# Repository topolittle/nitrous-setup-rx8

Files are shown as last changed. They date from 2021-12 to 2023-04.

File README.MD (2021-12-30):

# Nitrous Oxide System installation for the Maxda RX-8

I wanted a nice and clean installation for my Nitrous Oxide System in my car. My installation has the following components:
- Main kit
- Bottle heater
- Purge
- NOS pressure sensor and gauge
- Fuel pressure sensor and gauge
- Oil pressure sensor and gauge
- Oil temperature sensor and gauge

Each components comes with wires and switches, so at the end of the day you end-up with a cockpit full of holes and different looking switches all over the place.

My goal for this project was to have all the system controls and gauges at the same place, under the original ashtray cover. I wanted also something that was easily serviceable. For example if I need to remove a sensor, I should be as easy as any other factory components.

There is two 3D printed components, one for the main control board and the other one for the head unit, in place of the ashtray. The parts were printed in ASA since it can support high and freezing temperature without deforming.

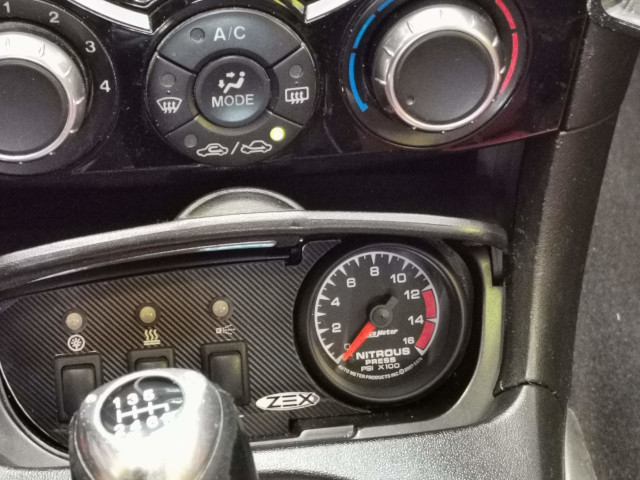
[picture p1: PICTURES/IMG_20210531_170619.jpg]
Ashtray


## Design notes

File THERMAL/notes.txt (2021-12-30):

Thermal managment:
Power to dissipate inside the enclosure: 200mA * 12V = 2.4W
Surface area of the enclosue: 0.4 ft-sqr
Watt per square foot: 6
Temperature rise: 15.5C (approx)
Expected max ambiant: 40C, so it gives us a max temperature of 55.5C inside the case,
just below of the glass transition temperature of the PLA which is 65C. ABS appears more suited for
this job since its glass transition temperature is around 105C.

Reference: https://safe.nrao.edu/wiki/pub/CICADA/GreenBankSpectrometer/Hoffman_Heat_Dissipation_Document.pdf

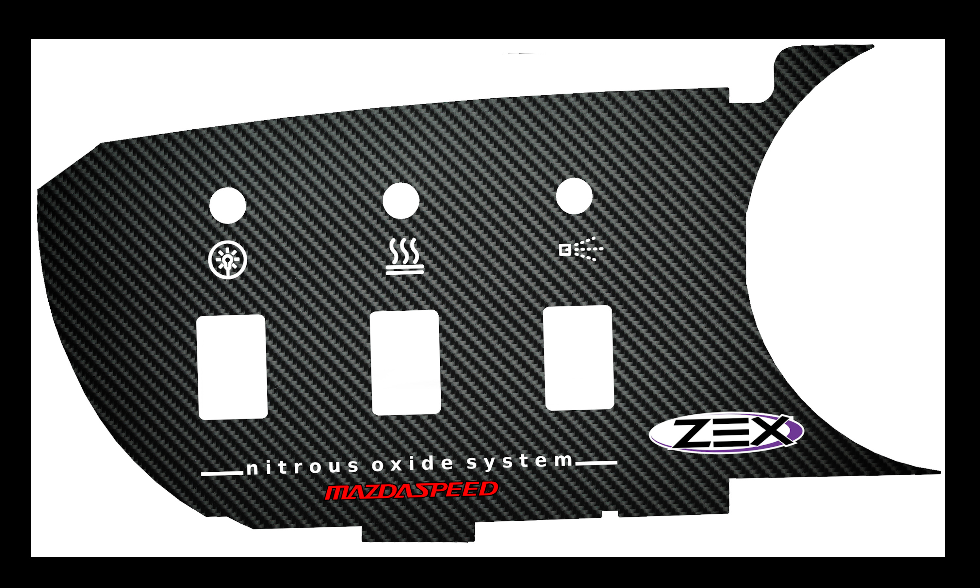
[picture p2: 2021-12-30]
ARTWORK/Nitrous_Artwork_v11_600dpi.jpg

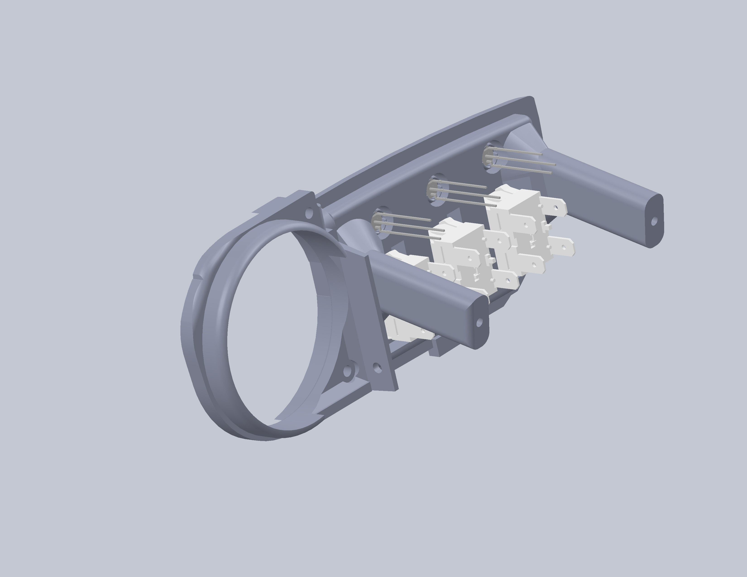
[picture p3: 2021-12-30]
MECHA/3D_MODEL/EXPORTS/front_panel_back.JPG

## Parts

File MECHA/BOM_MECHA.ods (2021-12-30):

Ordered | Where |  |  |  | Brand | Part No. | Autopartway | TDOT | Amazon | Garage16 | Notes
08/11/20 | Website | Lotek Gague pod w clamp and silicone | $100.00 | USD | Lo-Tek |  |  |  |  |  |  | http://www.gaugepods.com/mazda.html
08/12/20 | Garage16 | Prosport gauges oil pressure | $57.00 | USD | Prosport | 216BFWAOPSM.PSI | n/a | n/a | n/a | $104.50 |  | https://prosportgauges.com/collections/performance-series-amber-white/products/amber-white-2-1-16-electrical-oil-pressure-gauge
08/12/20 | Garage16 | Prosport gauges oil temp | $49.00 | USD | Prosport | 216BFWAOTSM.F |  |  | $85.00 | $85.00 |  | https://prosportgauges.com/collections/performance-series-amber-white/products/amber-white-2-1-16-electric-oil-temperature-gauge
08/18/20 | Garage16 | Prosport gauges fuel pressure
08/12/20 | Garage16 | Mishimoto Sandwish plate adaptor | $93.00 | CAD | Mishimoto | MMOP-TPS | n/a | $105.00 | $93.00 | $77.00 |  | https://www.mishimoto.com/oil-plate-sandwich-adapter.html#features | https://www.amazon.ca/-/fr/Mishimoto-MMOP-TPS-Sandwich-Plate-Adapter/dp/B004UVL6T4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
08/12/20 | Garage16 | Auto Meter 5974 Nitrous pressure gauge | $333.00 | CAD | Auto Meter | 5974 | 239 | 333 | 375 | 335 |  | https://www.tdotperformance.ca/auto-meter-5974-2-1-16-nitrous-0-1600-psi-es.html
08/20/20 | Julien | ZEX Nitrous kit 82021 | $950.00 | CAD |  |  | 924 |  |  |  |  | https://www.zex.com/wet-nitrous-system.html
08/12/20 | Garage16 | Vibrant 4 AN 1/8 npt adaptor | $13.00 | USD |  | 16484 | 16.63 | 40 | 40 | 21.12 | for nitrous line to pressure gauge | https://www.summitracing.com/parts/vpe-16484?seid=srese1
08/18/20 | Amazon | Aeromotive Fuel Line Adapter | $80.00 | USD |  | 15120 | n/a | n/a | $98.00 | n/a |  | https://black-halo-racing.myshopify.com/products/aeromotive-fuel-line-adapter
08/18/20 | Garage16 | vibrant 6an to 4an reducer |  |  |  | 10431
08/20/20 | Julien | Zex nitrous purge kit 82010 | $114.00 | USD |  |  |  |  |  |  |  | https://www.zex.com/nitrous-purge-kit.html
08/20/20 | Julien | Zex bottle heater 82006
 |  | Remote openner |  |  | Zex | 82009
08/17/20 | BHR | Throttle Body Spacer | 120 | USD
4 |  | M3 x 16mm button screw | for control unit enclosure
3 |  | M4 x 10mm button screw | for control unit pcb
2 |  | M3 x 10mm button screw | for head unit pcb
2 |  | M3 x 16mm button screw | for head unit fixation

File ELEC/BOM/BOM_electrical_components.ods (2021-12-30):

Qt | Part | Description | Digikey
3 | ACV31012 | RELAY AUTOMOTIVE SPST 20A 12V | 255-5270-ND
1 | G5V-1-2 DC12 | G5V-1-2 DC12 | Z3823-ND
1 | 1N4678 | Zener 1.8V | ‎641-MMSZ4678-HFCT-ND‎
1 | 2N3904
5 | 1N4007
4 | 4.7K | 1W | BC4534CT-ND
1 | 1K | 1/4W
1 | UBW1E101MPD1TD | 100uF/25V | 493-13149-1-ND
2 | FA26X8R1E105KNU06 | 1uF/25v Ceramic | 445-175056-1-ND
1 | PA414C1100 | SWITCH PUSH SPST-NO 16A 125V | PA414C1100-ND
2 | PA412C1100 | SWITCH PUSH DPST 16A 125V | EG4688-ND
3 | XLMDKCBD59M | LED BLUE/RED DIFF T-1 3/4 T/H | 1497-1018-ND
3 | 470 OHM / 1W | FMP200JR-52-470R | 470ZTR-ND
1 | 1723161114 | CONN HEADER R/A 14POS 3.5MM | WM11854-ND
1 | 1722583114 | CONN RCPT HSG 14POS 3.50MM | WM26323-ND
14 | 1722537023 | ULTRA-FIT TANGLESS CRIMP TERMINA | WM26316CT-ND
2 | 1722644007 | ULTRA-FIT TANGLESS TERMINAL POSI | WM26358-ND
3 | C-174 | LED HOLDER PNL CLIP 5MM BK NYL | 492-1781-ND
1 | 510360600 | CONN BOARD-IN HSG 6POS 4.00MM | WM17771-ND
6 | 500988000 | CONN PIN 18-22AWG CRIMP TIN | WM3312TR-ND
1 |  | 18 gauge wire 30 feet
1 |  | 14 gauge wire 30 feet
1 |  | 16 gage wire 20 feet
1 | 0532590629 | CONN HEADER R/A 6POS 3.5MM | WM14652-ND
1 | 510670600 | CONN RCPT HSG 6POS 3.50MM | WM3333-ND
6 | 502179101 | CONN SOCKET 18-24AWG CRIMP TIN | WM3318-ND

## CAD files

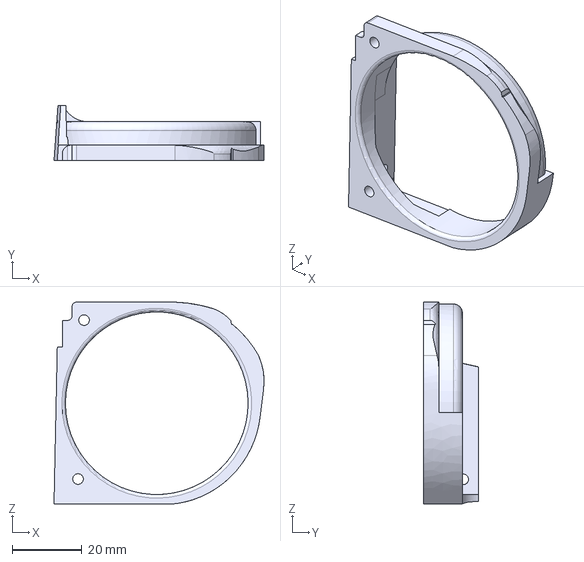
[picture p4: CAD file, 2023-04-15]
MECHA/3D_MODEL/STEP/pod_holder.step
60.2 x 15.9 x 57.8 mm

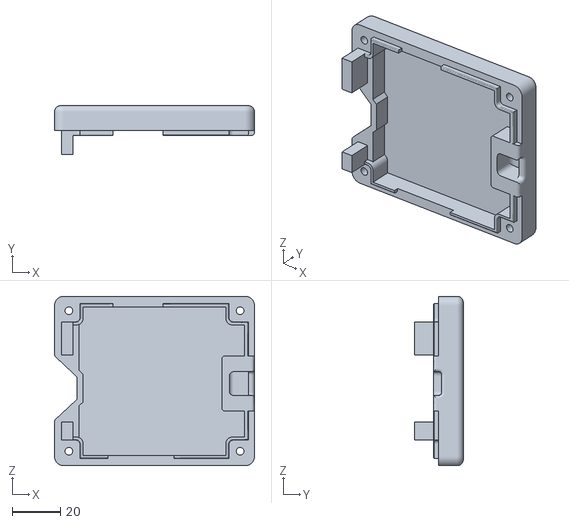
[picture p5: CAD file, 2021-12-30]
MECHA/3D_MODEL/STL/case_top.STL
82.8 x 20.2 x 70.1

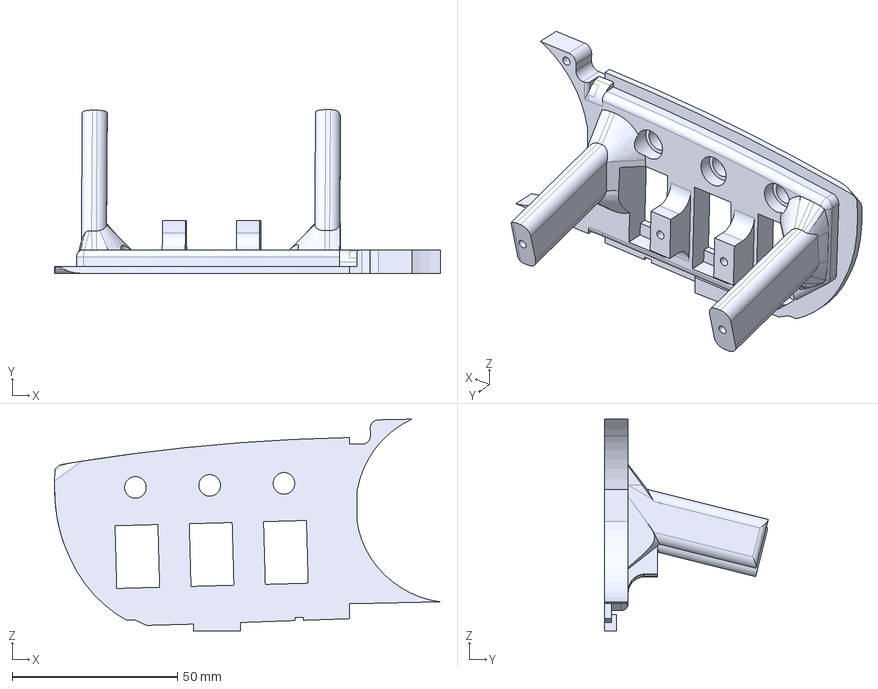
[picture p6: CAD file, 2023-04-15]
MECHA/3D_MODEL/STEP/front_plate.step
116.9 x 49.5 x 64.1 mm

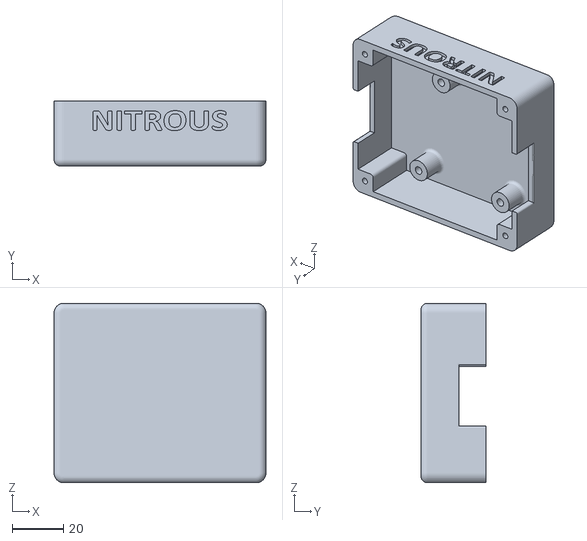
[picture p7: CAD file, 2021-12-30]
MECHA/3D_MODEL/STL/Case_bottom.STL
82.8 x 25.4 x 70.1

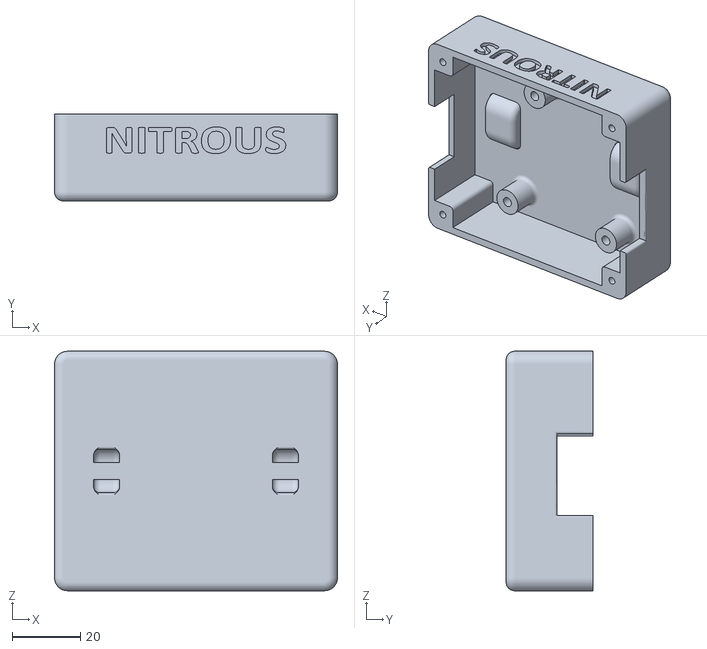
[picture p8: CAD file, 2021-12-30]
MECHA/3D_MODEL/STL/Case_bottom_v1.0.STL
82.8 x 25.4 x 70.1

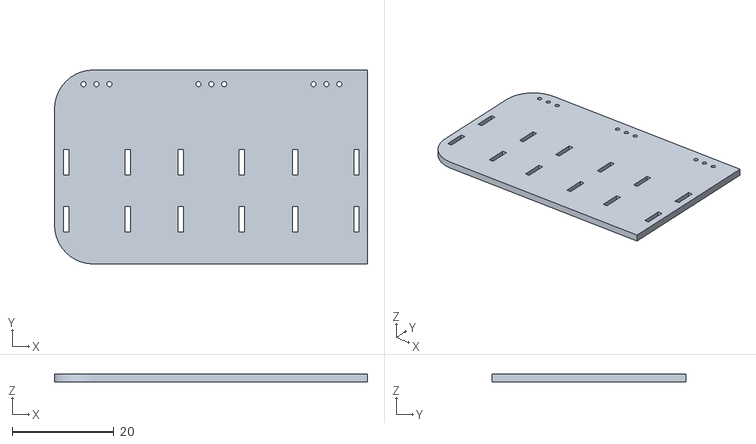
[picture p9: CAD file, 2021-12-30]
MECHA/3D_MODEL/STL/head_pcb.STL
61.5 x 38.1 x 1.57

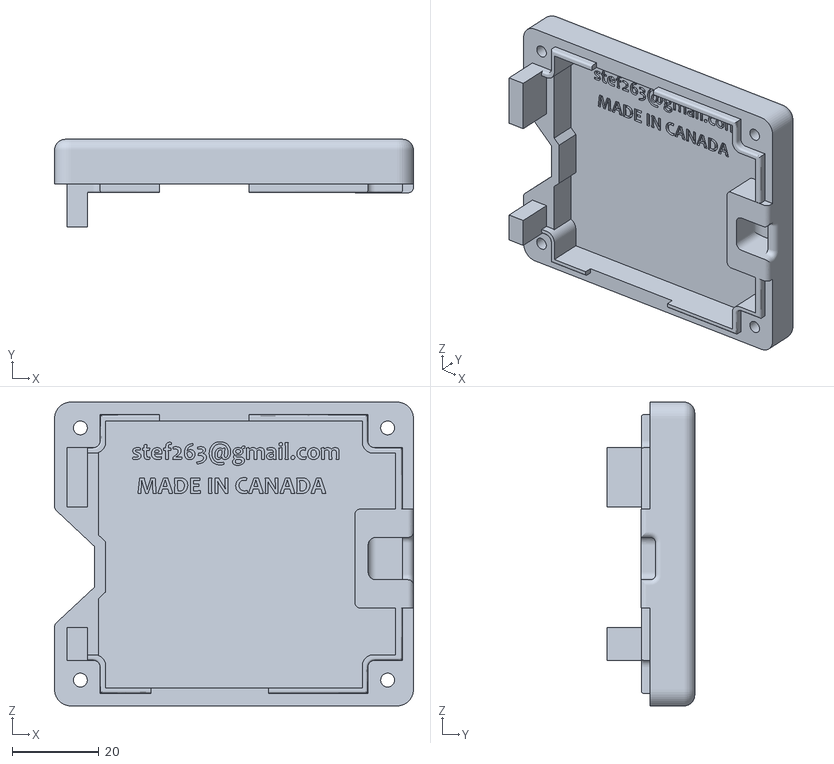
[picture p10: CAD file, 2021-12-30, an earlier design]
MECHA/3D_MODEL/STL/case_top_v1.1.STL
82.8 x 20.2 x 70.1

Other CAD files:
MECHA/3D_MODEL/STL/case_top_v1.2.STL
MECHA/3D_MODEL/STL/case_top_v1.0.STL
MECHA/3D_MODEL/STL/front_plate.STL
MECHA/3D_MODEL/STL/pod_holder.STL

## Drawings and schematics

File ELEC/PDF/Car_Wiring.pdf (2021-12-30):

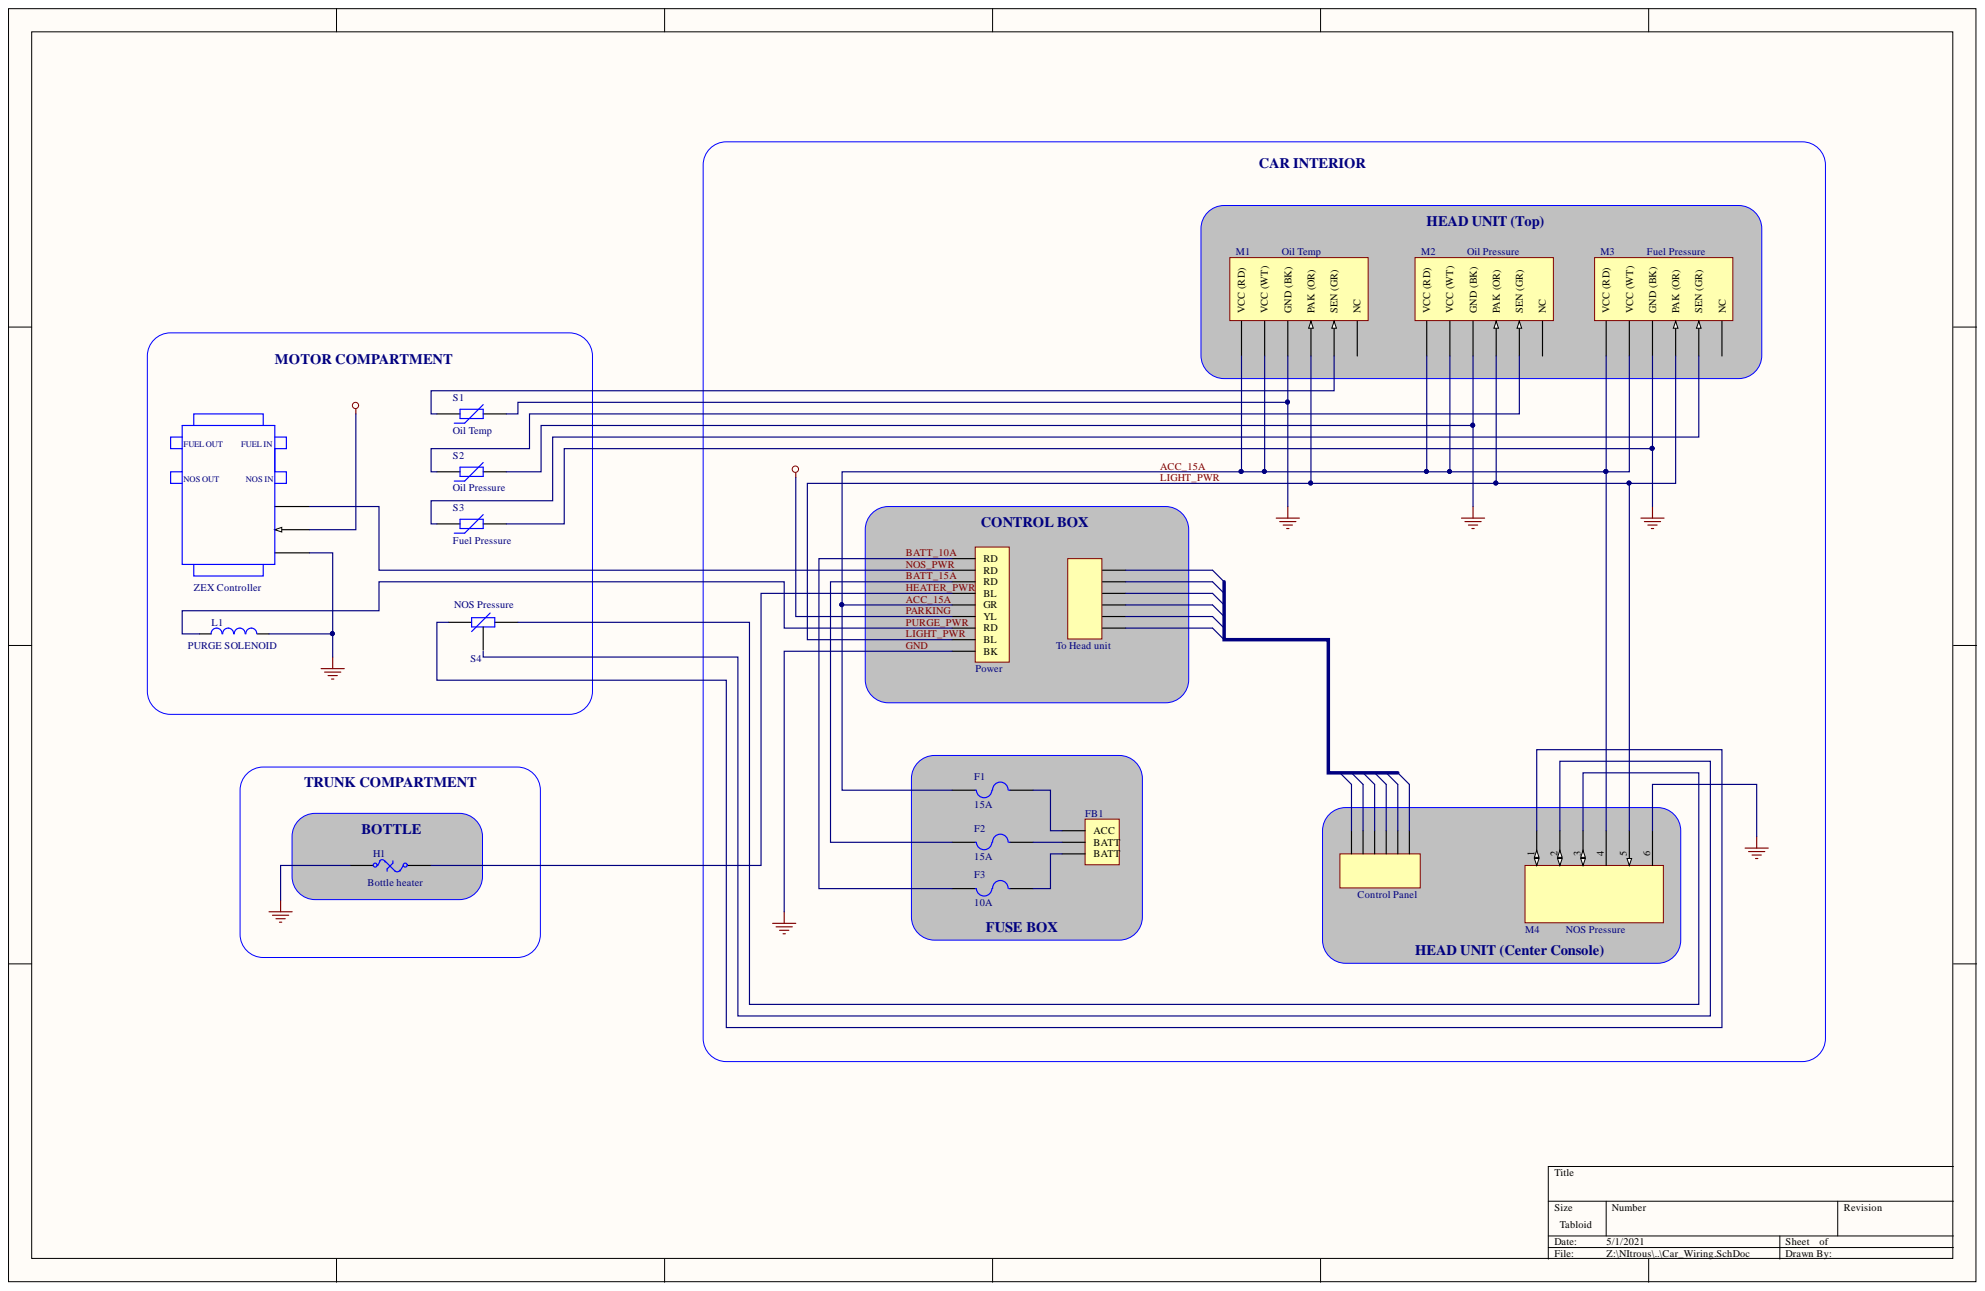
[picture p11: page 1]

Oil Pressure | | ACC_15A

LIGHT_PWR

CONTROL BOX

HEATER_PWR
ACC_15A
PARKING | | YL RD BL
PURGE_PWR
GND | | BK

HEAD UNIT (Center Console)

Size Tabloid | Number | Revision

Date: 5/1/2021 | Sheet of
File: Z:\NItrous\..\Car_Wiring.SchDoc | Drawn By:

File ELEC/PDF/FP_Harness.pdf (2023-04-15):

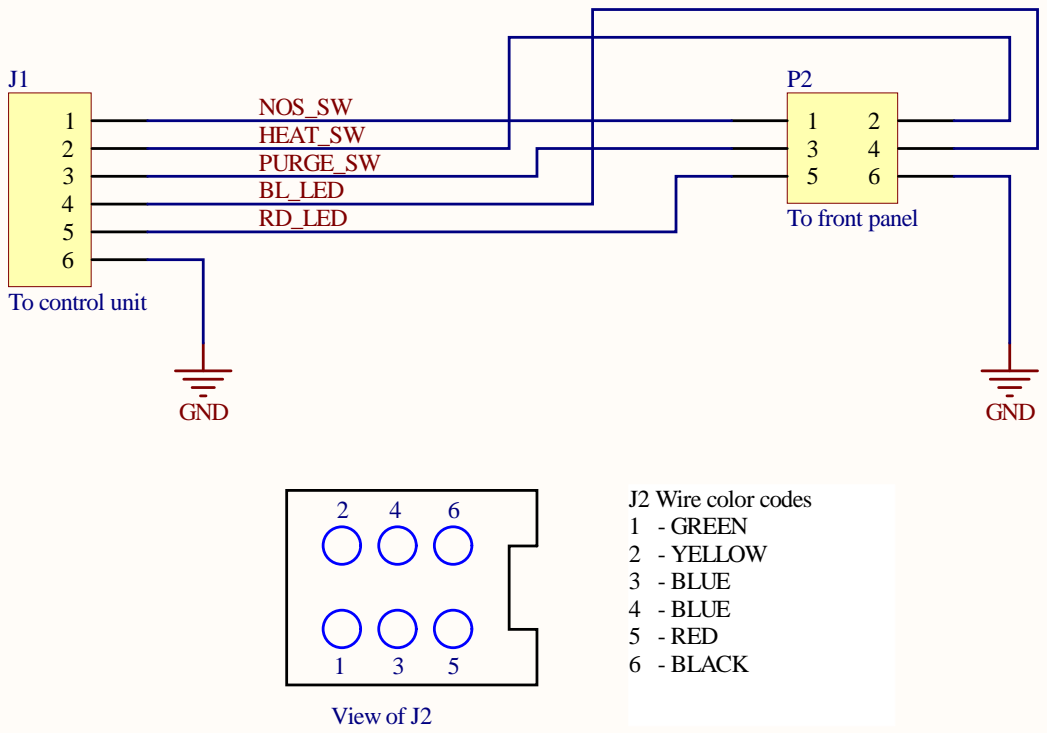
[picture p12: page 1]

HEAT_SW
PURGE_SW
BL_LED

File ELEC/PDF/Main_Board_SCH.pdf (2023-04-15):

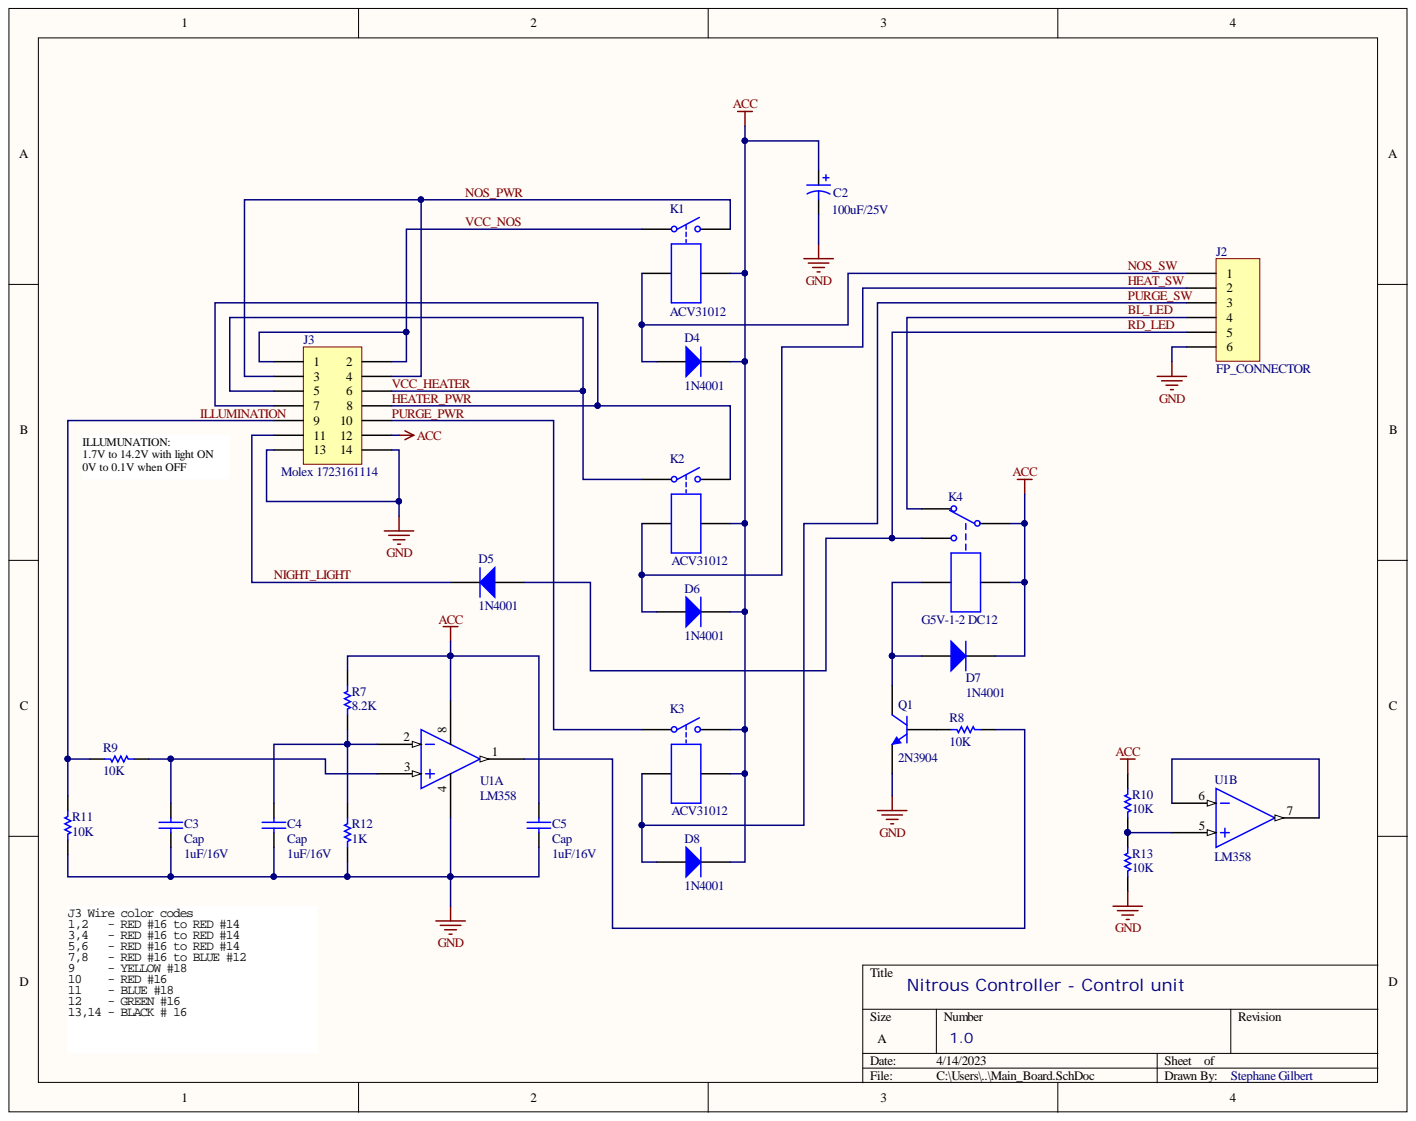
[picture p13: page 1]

1 0 1 2 | GND HEAT_ S W

7 8 | HEATER_P
9 1 0 | GE_PWR

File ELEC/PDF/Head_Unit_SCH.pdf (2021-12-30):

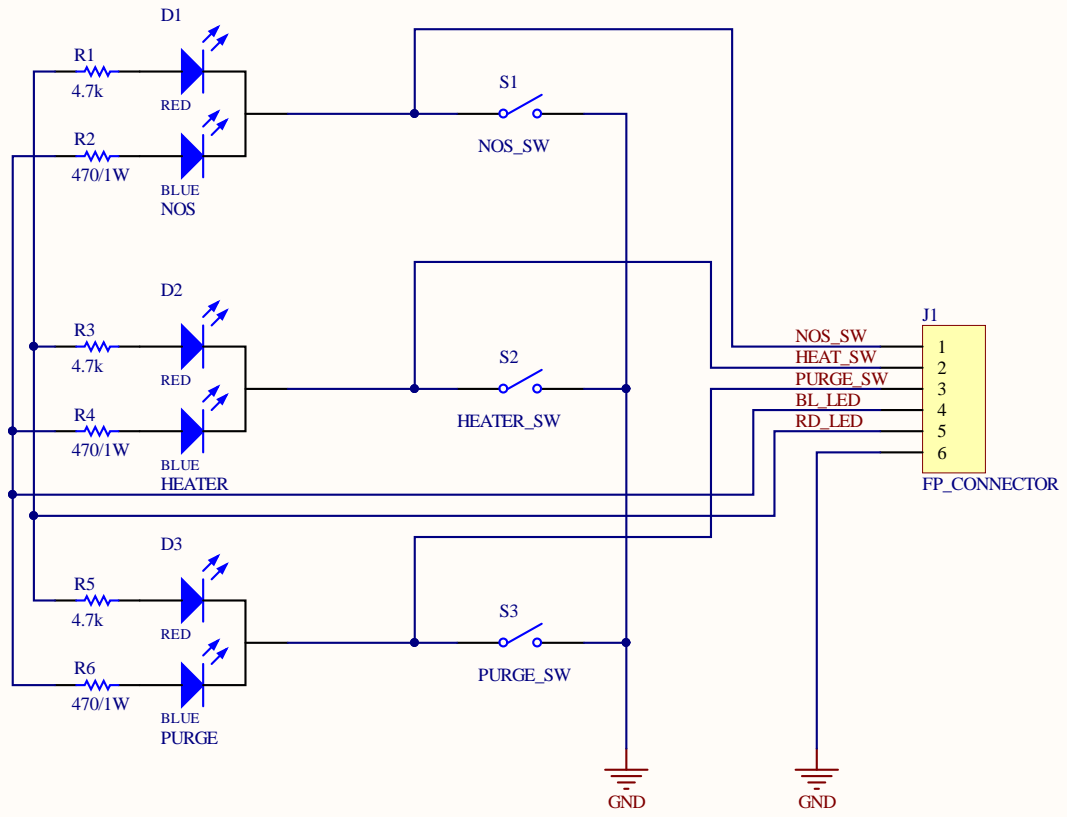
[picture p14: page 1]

NOS_SW

S2 | HEAT_SW PURGE_SW

BL_LED

R4 | | HEATER_SW | RD_LED

BLUE HEATER

Title
Nitrous Controller- Head unit

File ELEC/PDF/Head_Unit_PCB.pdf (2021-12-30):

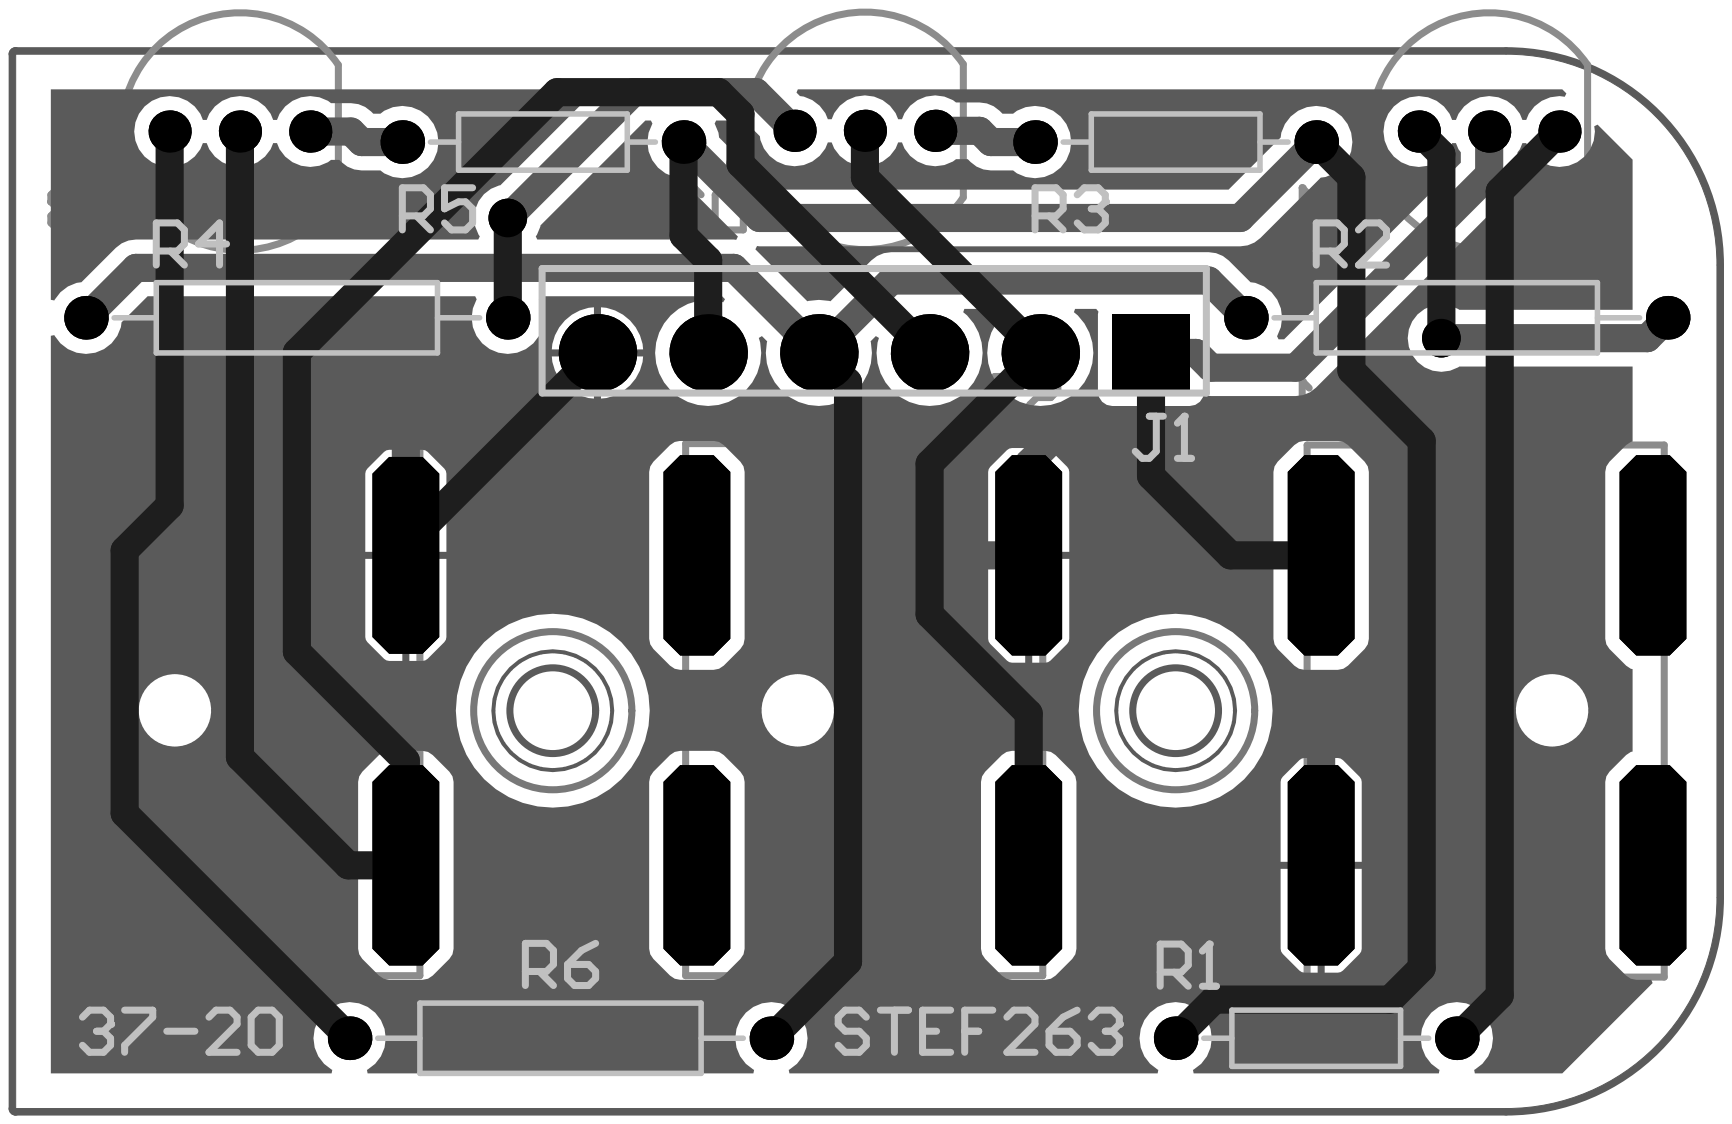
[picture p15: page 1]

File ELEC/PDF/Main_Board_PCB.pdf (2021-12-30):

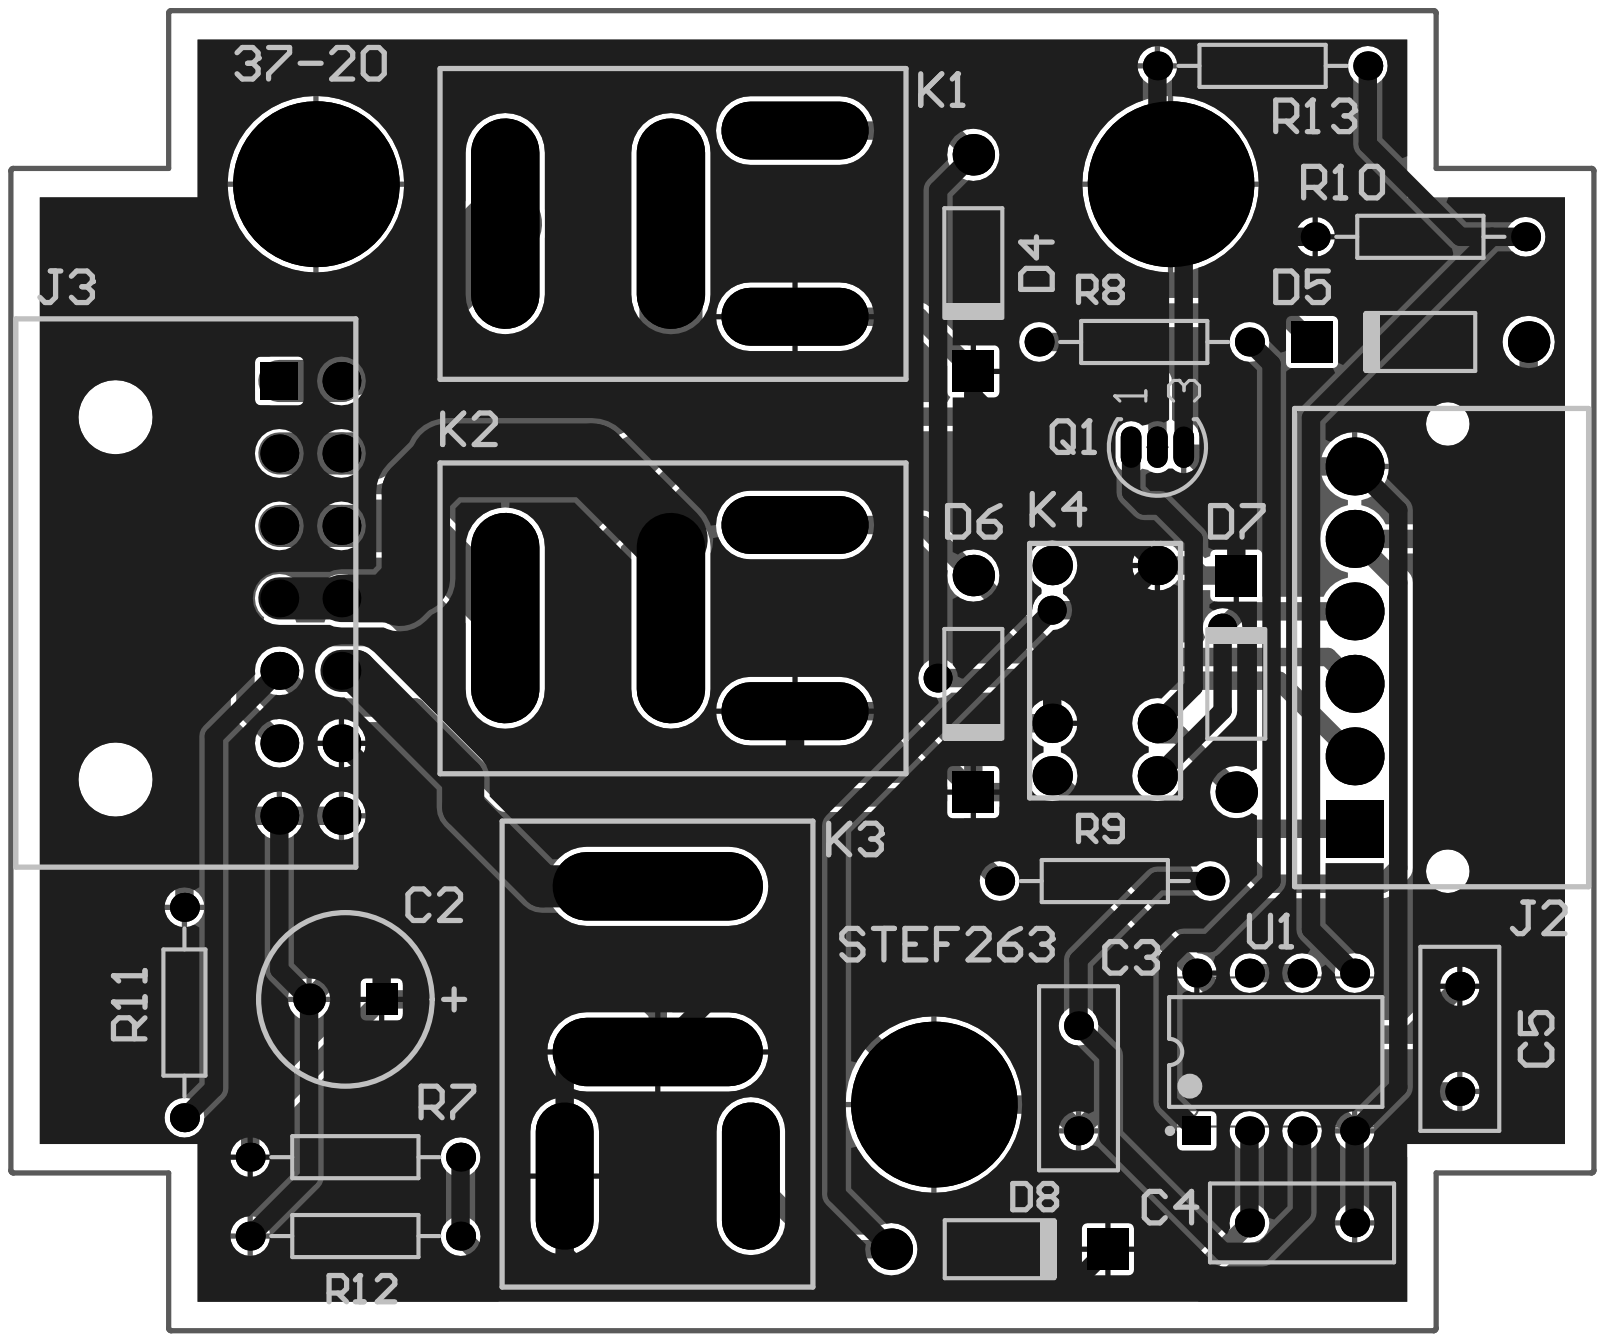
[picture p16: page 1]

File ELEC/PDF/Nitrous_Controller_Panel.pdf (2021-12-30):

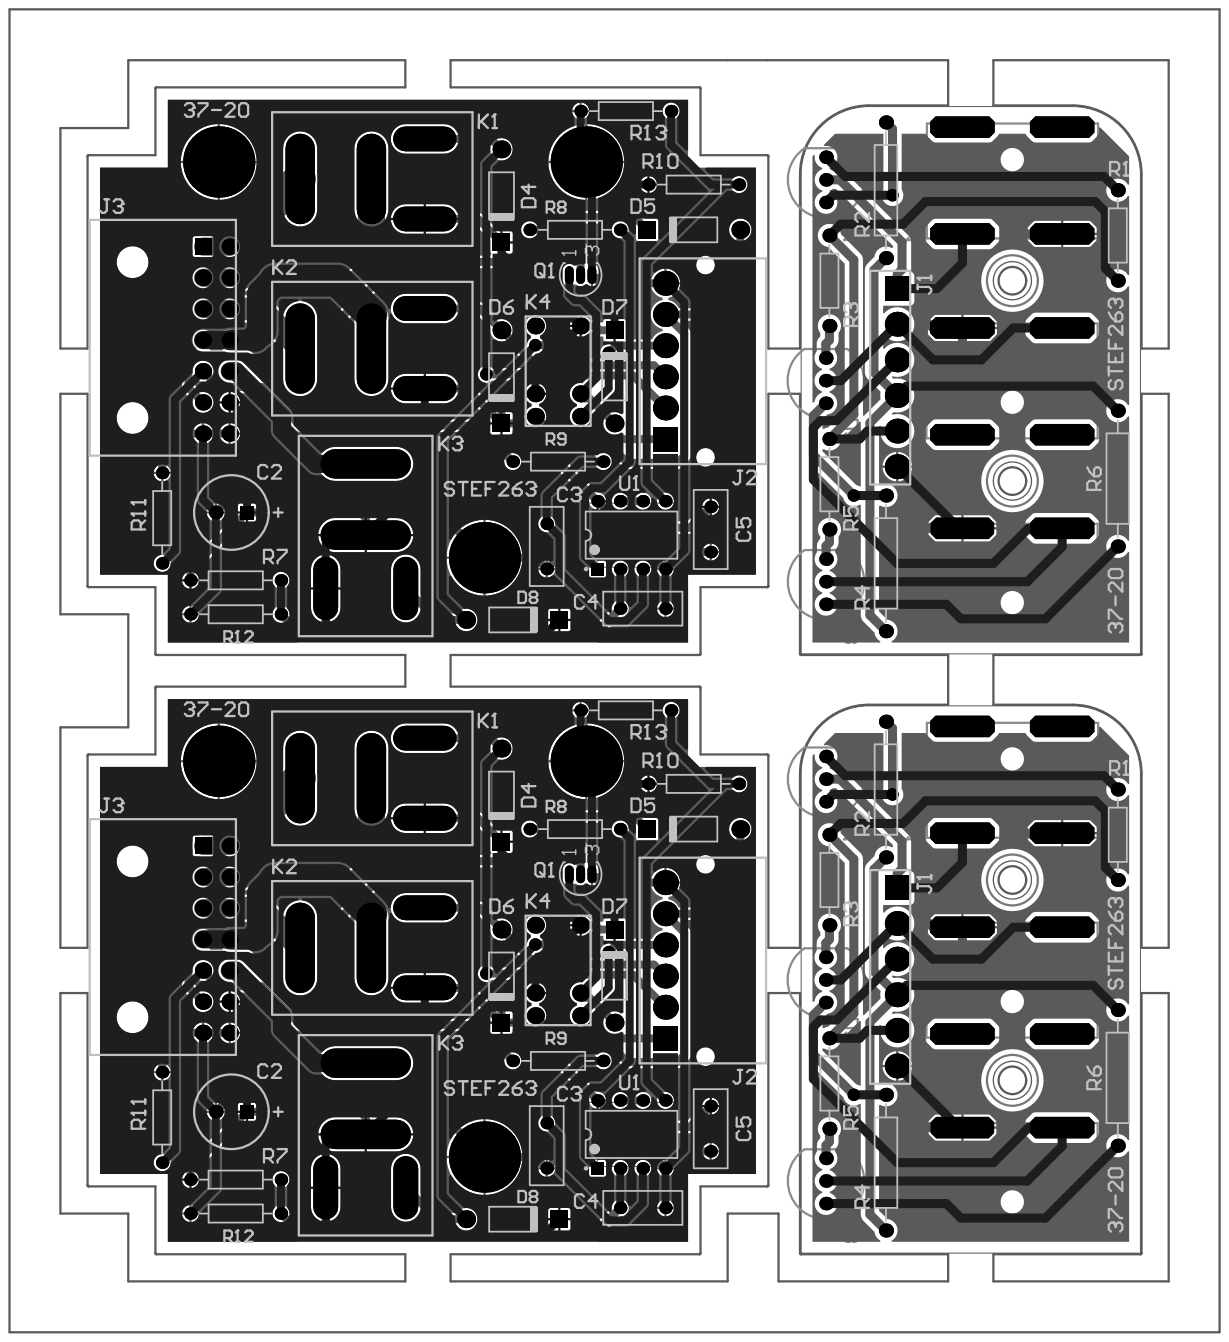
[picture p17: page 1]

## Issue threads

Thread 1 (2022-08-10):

3D Model Source Files

jrhodnik, 2022-08-10:
Greetings!

Could you possibly upload the model files as STEP? I'd like to modify your design to instead hold some normal 12v accessories, similar to [this one](https://www.thingiverse.com/thing:2720594). Unfortunately, that ones's for a newer RX8 so it's not compatible with mine. I plan to upload the modified version to Thingiverse after it's complete, along with model source files as well.

Thank you kindly!

jrhodnik, 2022-08-10:
I have access to both Fusion 360 and Onshape, both of which apparently have support for Solidworks files.

Thank you for your response!

topolittle, 2022-08-10:
Hi John,

I tried to send you the project by email but the file is too large. So here
is the file on my Dropbox:
https://www.dropbox.com/s/ot5q8igk4lx34mj/ashtray_solidworks.zip?dl=0

The parts you are looking for are front_plate.sldprt and pod_holder.sldprt.
You can also open the file fron_panel.sldasm which is an assembly of the
two parts.

Let me know if you have any questions. In the meantime I will try to upload
the steps files to Thingiverse.

Stephane

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

jrhodnik, 2022-08-11:
Hey Stephane,

This worked great! I was able to convert the `sldprt` files to `STEP` files using Onshape's free trial. It is also apparently possible using Fusion 360, but you gotta pay for that. And I'm just a hobbyist, so it didn't make much sense for me to do so.
[For anyone who needs the `STEP` files, here they are.](https://github.com/topolittle/nitrous-setup-rx8/files/9308835/Converted.zip)

I did modify them and made a simple flat template that can be modified with whatever people would like,, but I'm unable to test it as I don't actually have an ash tray for my car just yet. The goobers that owned it before me ripped a bunch of stuff out of the interior 😞. Once I get an ashtray I'll give it a test.

Onwards and upwards!

Closed 2022-08-12.

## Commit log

2022-08-13 Added STEP files provided by jrhodnik
    fixes #1
    [front_plate.step, pod_holder.step]
2023-04-15 Added missing schematic PDF
